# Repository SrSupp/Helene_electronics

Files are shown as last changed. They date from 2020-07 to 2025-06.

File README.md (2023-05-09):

Author: Sven Suppelt, Felix Herbst		Date: 09.05.2023


# HELENE - electronics for the low cost 6DOF robot
This repository is responsible for the electronics for the Helene robotarm. Included are the PCBs and the code to run on these. 

The robot arm has a motor control board on each of its 6 axes. The board of the lowest axis, the 1st axis, acts as ROS Serial Slave. All other axes receive their control data from the 1st axis via CAN. 

A single motor control board consists of a microcontroller (ESP32), a stepper motor driver (TMC5160), a magnetic encoder to determine the current position of the robot arm (AS5048) and a CAN transceiver. 
The 1st axis is equipped with an external magnetic encoder due to lack of space. All other axes have enough space so that the board can be mounted directly above the required magnet. 

# Folder structure
The boards are located in the folder "pcb". Here you will find the board for the external encoder and the motor control board. The source code for the boards can be found in the "code" folder. Stored there are the PlatformIO projects for the ROS Serial Slave (Helene_ESP_Master) and the other boards connected via CAN (Helene_ESP_Slave).
In the pcb folder there are two additional optional boards, the end effector board and a H-bridge with voltage converter. The end effector board has its own ESP32 with an ADC for measuring load cells. Furthermore, two outputs for servos are provided, so that grippers with integrated force measurement can be realized. The H-bridge is connected via the expansion ports on the boards and can drive motors up to 3A at 5V. It does not have its own microcontroller.

# System structure of the robot arm
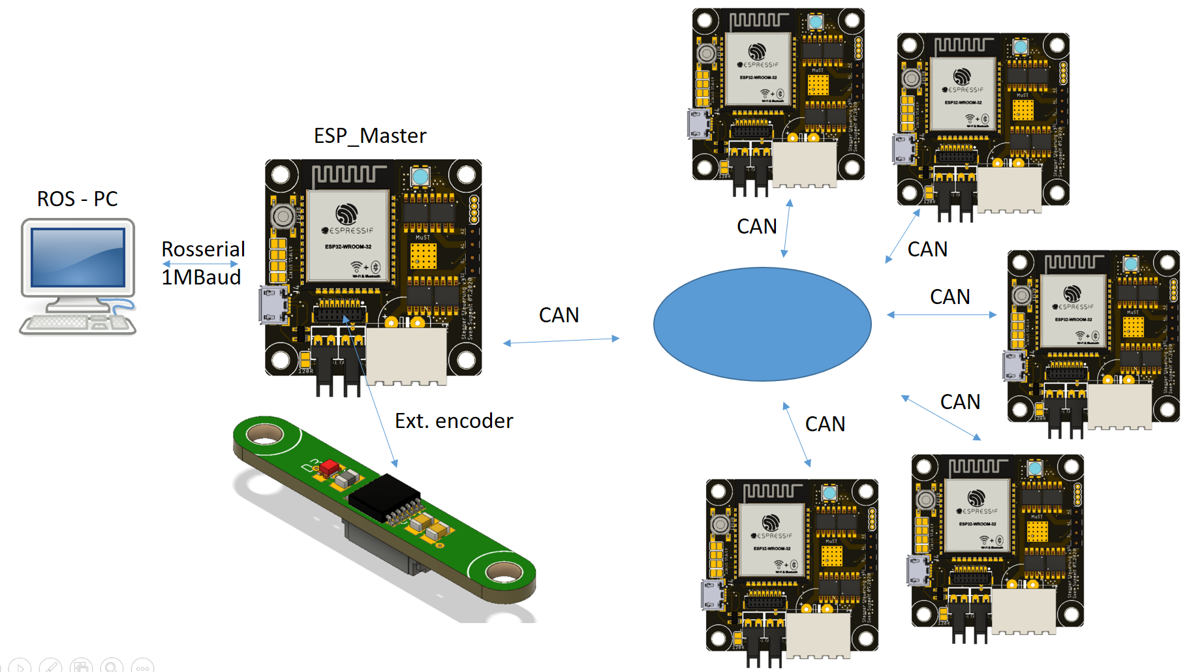
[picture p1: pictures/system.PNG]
 

# Available Serial Commands
Each slave is equipped with the possibility of serial communication. Via this interface the calibration value of each axis can be read and set and status information can be read out. It is absolutely necessary to calibrate each axis individually!
The following commands are available:

long form | short form | description
-------- | -------- | --------
*IDN? | IDN? | Prints identification
HELP? | HELP | Prints a help screen (not yet implemented)
CALSINGLEJOINT [joint ID] | CAJO [joint ID] | starts the calibration process of given joint. Instructions will be printed after that command!
SETNULL [0,1] | SENU [0,1] | globally enables (1) or disables (0) the Nullpunktfahrt at startup
GETCALVALUE [joint ID] | GECA [joint ID] | Prints the current saved calibration value of given joint
SETCALVALUE [joint ID] | SECA [joint ID] | Sets the current saved calibration value of given joint. Instructions are printed after that command!
GETACTUAL [joint ID] | GEAC [joint ID] | Prints the actual angle of given joint. The actual angle is: Raw_Angle - Calibration_Value
GETRAW [joint ID] | GERA [joint ID] | Prints the raw angle of given joint
DONULL [joint ID] | DONU [joint ID] | The given joint will do a Nullpunktfahrt
OFFANDNULL [joint ID] | OFNU [joint ID] | Sets a offset value on the current calibration value. After that a Nullpunktfahrt is initiated. Instructions are printed out!
DIAG | DIA | Prints out diagnose data

# Installation instructions

1. Gather all materials.
You will need 6 motor control boards and 1 external encoder board.
2. Do the wiring. 
You will have to run CAN and power to each motor control board. The boards are daisy-chainable!
3. Program the boards.
"Helene_ESP_Master" should be uploaded to the board in joint 1. This board is configured with rosserial so that it communicates directly with ROS.
"Helene_ESP_Slave" should be uploaded to the boards in joint 2-6. These boards talk via CAN to the board in Joint 1 and thus receive their control information. With each individual board it is possible to calibrate the robot arm. 
After programming, each board should slowly blink red!
4. Set the SMD-Jumpers.
For joints 1 and 6 the CAN terminating resistor must be set by bridging the SMD solder bridge next to the CAN sockets.
Additionally the Joint-ID must be set for each board. For this purpose four SMD pads are provided next to the USB socket. By bridging these pads the ID can be set. The data format is binary with the most significant bit first. For example the joint 5: 0 1 0 1 must be set. 
5. Calibrate the zero position
6. Enable Nullpunktfahrt globally

# Video installation instructions

The installation process is also explained in the following video.
(http://www.youtube.com/watch?v=I9vXAa9pZOI "")
Starting at 0:09 the installation of the electronics is explained. From 6:21 on the calibration is shown.

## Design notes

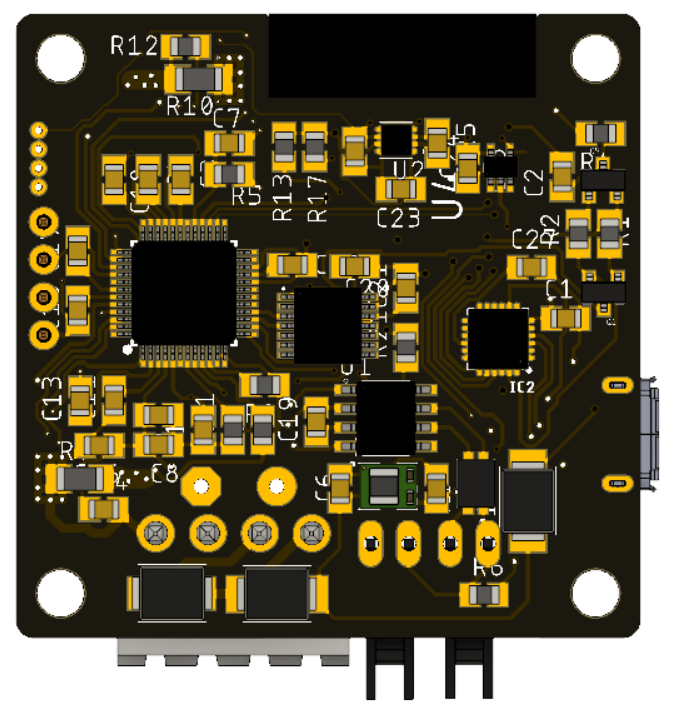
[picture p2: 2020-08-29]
pictures/Motorsteuerung_back.PNG

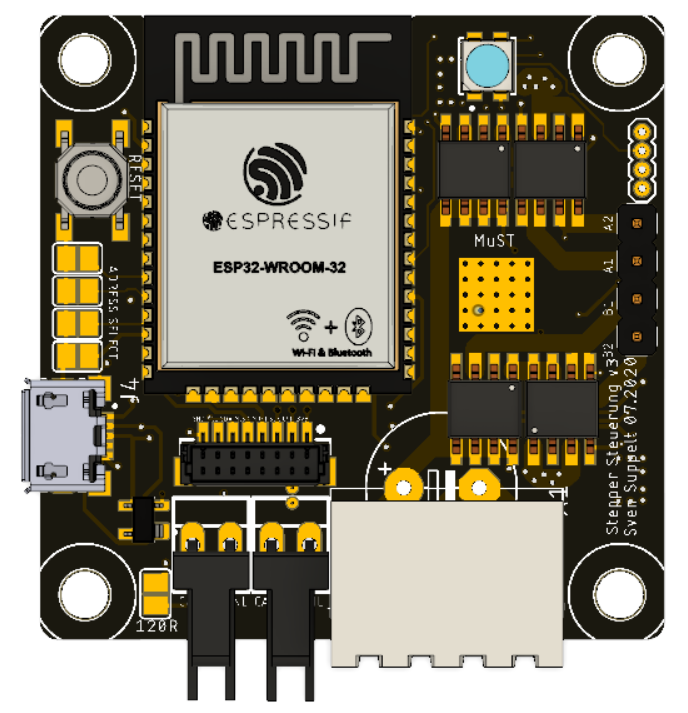
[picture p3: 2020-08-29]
pictures/Motorsteuerung_front.PNG

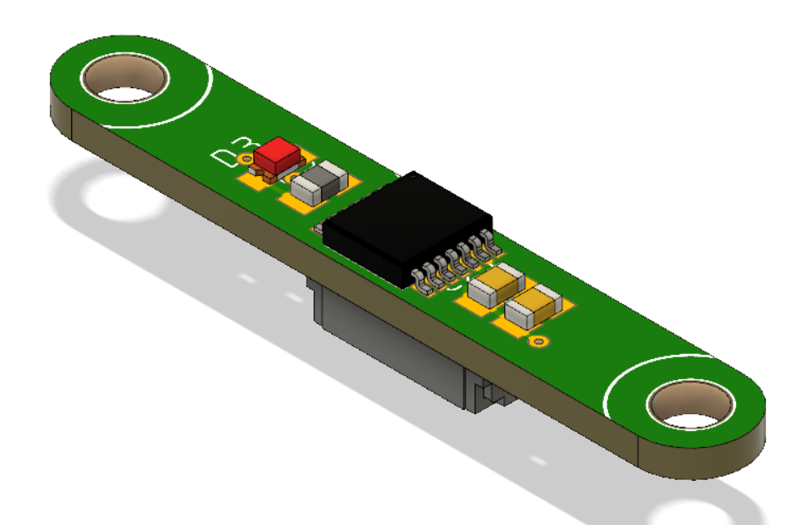
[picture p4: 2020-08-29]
pictures/ext_encoder.PNG

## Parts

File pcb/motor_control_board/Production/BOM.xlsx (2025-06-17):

 |  |  | Motorsteuerung V3 BOM
Item # | *Designator | *Qty | Manufacturer | *Mfg Part # | Description / Value | *Package/Footprint | Type | Your Instructions / Notes
1 | C1, C20 | 2 | Murata | GRM21BR6YA106KE43L | 10uF 0805 min.5V | 0805 | SMD
2 | C2, C25 | 2 | KEMET | C0805C105K4RAC7210 | 1uF 0805 min. 5V | 0805 | SMD
3 | C3 | 1 | Yageo | CC0805KRX7R0BB223 | 22nF 0805 100V | 0805 | SMD
4 | C4, C12, C13, C15, C17, C18, C19, C21, C26 | 9 | KEMET | C0805C104J5RACAUTO | 100nF 0805 | 0805 | SMD
5 | C5 | 1 | Taiyo Yuden | JMK212BJ476MG-T | 47uF 0805 min 4V | 0805 | SMD
6 | C6, C23, C24, C27 | 4 | Taiyo Yuden | UMK212BBJ475MG-T | 4,7uF 0805 min 5V | 0805 | SMD
7 | C7, C14, C16 | 3 | KEMET | C0805C474K5RAC7210 | 470nF 0805 min 25V | 0805 | SMD
8 | C8, C9 | 2 | Murata | GRM21BR6YA106KE43L | 10uF 0805 min 25V | 0805 | SMD
9 | C10, C11 | 2 | Taiyo Yuden | UMK212ABJ225KG-T | 2,2uF 0805 min 12V | 0805 | SMD
10 | C22 | 1 | Do not equip | Do not equip | Do not equip | Do not equip | THT | Do not equip
11 | R1, R2 | 2 | Yageo | RC0805FR-071KL | 1k 0805 | 0805 | SMD
12 | R4, R13, R17 | 3 | Yageo | RC0805JR-0710KL | 10k 0805 | 0805 | SMD
13 | R5 | 1 | CR0805-J/-2R2ELF | Bourns | 2,2 Ohm 0805 | 0805 | SMD
14 | R6 | 1 | Yageo | RC0805FR-07120RL | 120 Ohm 0805 | 0805 | SMD
15 | R7, R10 | 2 | Yageo | RL1206FR-070R075L | 75mOhm 1206 | 1206 | SMD | Messshunt
16 | R8, R9, R11, R12, R21 | 5 | Panasonic | ERA-6AEB49R9V | 49,9 Ohm 0805 | 0805 | SMD
17 | D1, D2 | 2 | Multicomp | SS34A | SMB Shottky Diode | SMB | SMD
18 | D3 | 1 | Adafruit Industries | 2659 | 2659 Adafruit LED | 2659 | SMD
19 | D7 | 1 | Littlefuse | SP0503BAHTG | USB ESD Schutz | SOT143 | SMD
20 | D10 | 1 | Diodes Inc. | SMBJ30AQ-13-F | TVS Diode | SMBJ | SMD
21 | IC1 | 1 | Trinamic | TMC5160-TA-T | Motortreiber IC | TQFP48-EP | SMD
22 | IC2 | 1 | Solicon Labs | CP2104-F03-GM | USB Seriell Wandler | QFN24_4MM_SMSC | SMD
23 | J1 | 1 | Do not equip | Do not equip | Do not equip | Do not equip | THT
24 | J2 | 1 | JST | BM08B-SRSS-TB(LF)(SN) | 8 Port SMD stehende Buchse |  | SMD
25 | J3 | 1 | Do not equip | Do not equip | Do not equip | Do not equip | THT
27 | J4 | 1 | Amphenol FCI | 10118193-0001LF | USB-Stecker 5P MICRO USB TYPE B RECEPTACLE W/ PEGS | FCI_10118193-0001LF | SMD
28 | PS1 | 1 | Texas Instruments | LMZM23600V3SILR | 3,3V Spannungswandler |  | SMD
29 | Q1, Q2, Q3, Q4 | 4 | Alpha&Omega | AO4882 | Dual N-Ch Mosfet | SOIC8 | SMD
30 | Q5, Q6 | 2 | ON Semiconductor | BC817-16LT1G | NPN Transistor | SOT23-3 | SMD
31 | SJ1, SJ2 | 2 | Do not equip | Do not equip | Do not equip | Do not equip | SMD | Do not equip
32 | SJ5, SJ6, SJ7, SJ8, SJ9 | 5 | Do not equip | Do not equip | Do not equip | Do not equip | SMD | Do not equip
33 | SW1 | 1 | E-Switch | TL3342F160QG | Taster |  | SMD
34 | U1 | 1 | Texas Instruments | SN65HVD232DR | Can Treiber | SOIC127P600X175-8N | SMD
35 | U2 | 1 | Texas Instruments | LM2775QDSGTQ1 | 3,3V zu 5v | SON50P200X200X80-9N | SMD
36 | U3 | 1 | ams | AS5048A-HTSP-500 | Magnetencoder | SOP65P640X120-14N | SMD
37 | U4 | 1 | Nexperia | 74HCT1G08GW,125 | And Gate | SOT65P210X110-5N | SMD
38 | X1 | 1 | Do not equip | Do not equip | Do not equip | Do not equip | THT | Do not equip
39 | X2 | 1 | Espressif Systems | ESP32-WROOM-32 | Microprozessor |  | SMD
40 | X6, X7 | 2 | Do not equip | Do not equip | Do not equip | Do not equip | THT | Do not equip
41 | FL1 | 1 | Murata | DLW32SH220XK2L | Gleichtaktdrosseln / Filter 1210 80VDC 22uH 250mA AEC-Q200 | 1210 | SMD

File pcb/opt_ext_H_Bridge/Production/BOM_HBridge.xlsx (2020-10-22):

 |  |  | External H Bridge BOM
Item # | *Designator | *Qty | Manufacturer | *Mfg Part # | Description / Value | *Package/Footprint | Type | Your Instructions / Notes
1 | C20 | 1 | Murata | GRM21BR6YA106KE43L | 10uF 0805 min.5V | 0805 | SMD
2 | C21 | 1 | KEMET | C0805C104J5RACAUTO | 100nF 0805 | 0805 | SMD
3 | U4 | 1 | Nexperia | 74LVC1G08GW,125 | And Gate | SOT65P210X110-5N | SMD
4 | J1,J2 | 2 | JST | BM08B-SRSS-TB(LF)(SN) | 8 Port SMD stehende Buchse |  | SMD
5 | U10 | 1 | ON Semiconductor | LM2576D2TR4-5G | Schaltspannungsregler 5V 3A Buck PWM |  | SMD
6 | L1 | 1 | Coilcraft | MSS1038T-104MLC | Festinduktivitäten 100uH Shld 20% 1.45A 304mOhms AECQ2 |  | SMD
7 | D4 | 1 | Vishay Semiconductors | SS36-E3/57T | Schottky Dioden & Gleichrichter 3.0 Amp 60 Volt |  | SMD
8 | C1,C31 | 2 | Nichicon | UCW1V221MNL1GS | Alu-Elektrolytkondensatoren - SMD 35volts 220uF AEC-Q200 |  | SMD
9 | U1 | 1 | Microchip Technology | TC4427VOA713 | Gate-Treiber 1.5A Dual |  | SMD
10 |  | 1 | Phoenix Contact | 1984617 | TERM BLK 2POS SIDE ENT 3.5MM PCB |  | THT
11 |  | 1 | Metz Connect | 31182104 | 4 Pos Header |  | THT
12 |  | 1 | JST Sales America Inc. | A08SR08SR30K152A | JUMPER 08SR-3S - 08SR-3S 6" |  | Kabel
13 |  | 2 | Metz Connect | 31169102 | 2 Pos Screw Terminal |  | Connector

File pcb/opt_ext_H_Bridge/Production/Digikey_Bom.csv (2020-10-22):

Manufacturer Part Number | Manufacturer | Digi-Key Part Number | Customer Reference | Reference Designator | Packaging | Part Status | Quantity | Unit Price | Extended Price | Quantity Available | Mfg Std Lead Time | Description | RoHS Status | Lead Free Status | REACH Status
74LVC1G08GW,125 | Nexperia USA Inc. | 1727-2872-1-ND |  |  | Cut Tape (CT) | Active | 1 | 0,18000 | 0,18 € | 27759 | 4 Weeks | IC GATE AND 1CH 2-INP 5TSSOP | ROHS3 Compliant | Lead free | REACH Unaffected
BM08B-SRSS-TB(LF)(SN) | JST Sales America Inc. | 455-1794-1-ND |  |  | Cut Tape (CT) | Active | 2 | 0,72000 | 1,44 € | 12416 | 16 Weeks | CONN HEADER SMD 8POS 1MM | RoHS Compliant | Lead free | Not Available
LM2576D2TR4-5G | ON Semiconductor | LM2576D2TR4-5GOSCT-ND |  |  | Cut Tape (CT) | Active | 1 | 1,97000 | 1,97 € | 1873 | 9 Weeks | IC REG MULTI CONFG 5V 3A D2PAK-5 | ROHS3 Compliant | Lead free | REACH Unaffected
SS36-E3/57T | Vishay Semiconductor Diodes Division | SS36-E3/57TGICT-ND |  |  | Cut Tape (CT) | Active | 1 | 0,43000 | 0,43 € | 11334 | 8 Weeks | DIODE SCHOTTKY 60V 3A DO214AB | ROHS3 Compliant | Lead free | REACH Unaffected
UCW1V221MNL1GS | Nichicon | 493-9430-1-ND |  |  | Cut Tape (CT) | Active | 2 | 0,60000 | 1,20 € | 28323 | 16 Weeks | CAP ALUM 220UF 20% 35V SMD | ROHS3 Compliant | Lead free | REACH Unaffected
TC4427VOA713 | Microchip Technology | TC4427VOA713CT-ND |  |  | Cut Tape (CT) | Active | 2 | 1,12000 | 2,24 € | 1871 | 8 Weeks | IC GATE DRVR LOW-SIDE 8SOIC | ROHS3 Compliant | Lead free | REACH Unaffected
1984617 | Phoenix Contact | 277-1721-ND |  |  | Box | Active | 1 | 0,41000 | 0,41 € | 12907 | 7 Weeks | TERM BLK 2POS SIDE ENT 3.5MM PCB | RoHS Compliant | Lead free | Not Available
A08SR08SR30K152A | JST Sales America Inc. | 455-3004-ND |  |  | Bulk | Active | 1 | 1,63000 | 1,63 € | 1113 | 12 Weeks | JUMPER 08SR-3S - 08SR-3S 6" | RoHS Compliant | Lead free | Not Available
CDRH10D60BT150NP-101MC | Sumida America Components Inc. | 308-CDRH10D60BT150NP-101MCCT-ND |  |  | Cut Tape (CT) | Active | 1 | 1,61000 | 1,61 € | 500 | Not Available | FIXED IND 100UH 2.3A 160MOHM SMD | ROHS3 Compliant | Not Available | Not Available

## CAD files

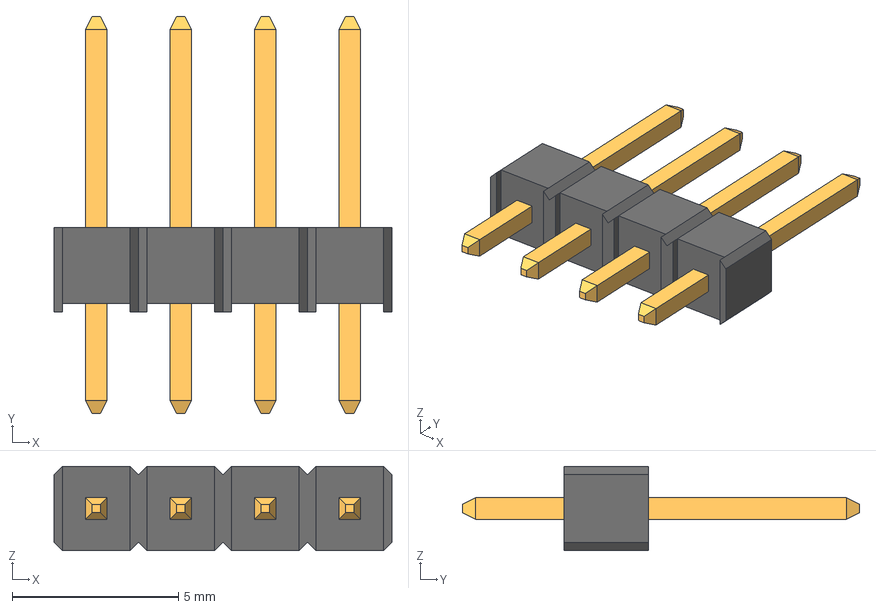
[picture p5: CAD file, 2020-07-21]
pcb/end_effector_board/PCB/zl201-4_p2-54_l10-2_w2-54_h8-89.stp
10.2 x 11.9 x 2.54 mm

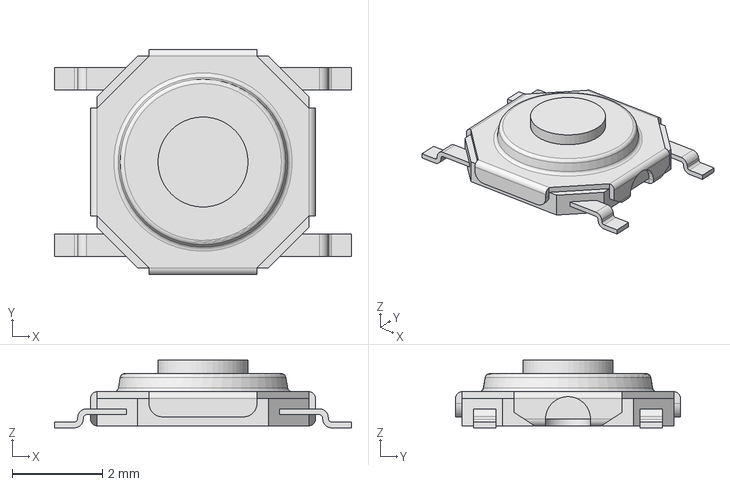
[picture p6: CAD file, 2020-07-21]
pcb/end_effector_board/PCB/TL3342FxxxQG.stp
6.60 x 5.00 x 1.50 mm

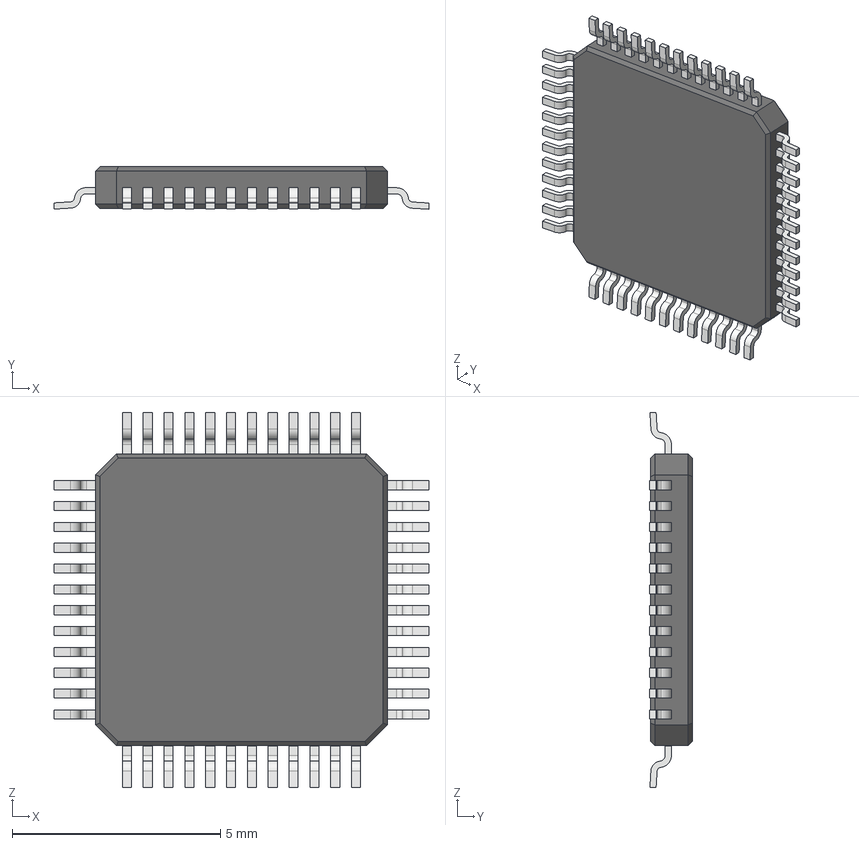
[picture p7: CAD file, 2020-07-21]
pcb/end_effector_board/PCB/TQFP48.step
9.00 x 1.02 x 9.01 mm

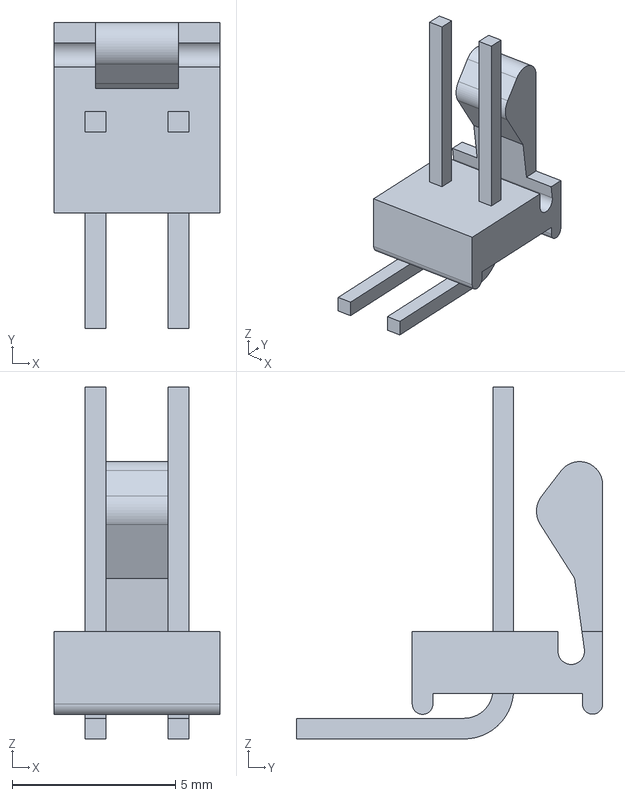
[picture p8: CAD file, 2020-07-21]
pcb/end_effector_board/PCB/c-640457-2-w-3d.stp
5.08 x 9.40 x 10.8 mm

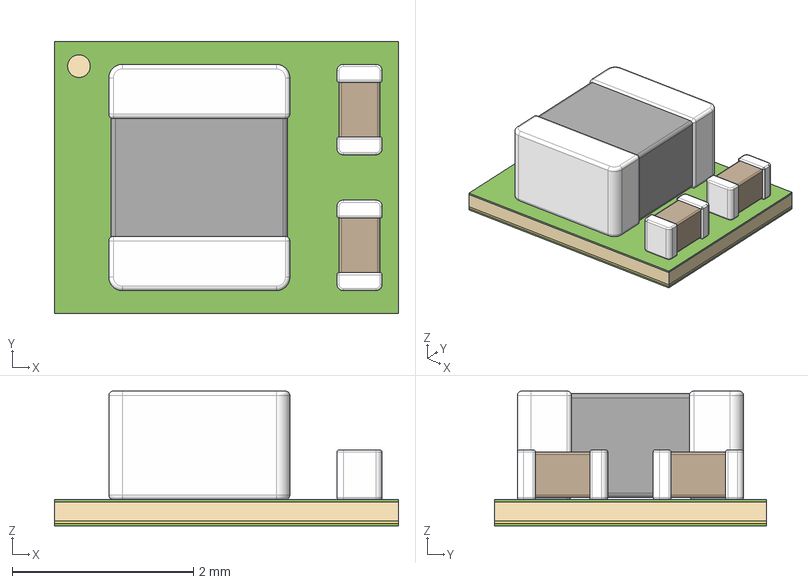
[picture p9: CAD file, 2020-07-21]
pcb/end_effector_board/PCB/LMZM23600.stp
3.80 x 3.00 x 1.49 mm
SOLDERMASK-BTM-SIL0010A
METAL-SIP
SUBSTRATE-SIP
SOLDERMASK-TOP
INDUCTOR-BODY
INDUCTOR-TERMNL x 2
CAP-BODY x 2
CAP-TERMNL x 4

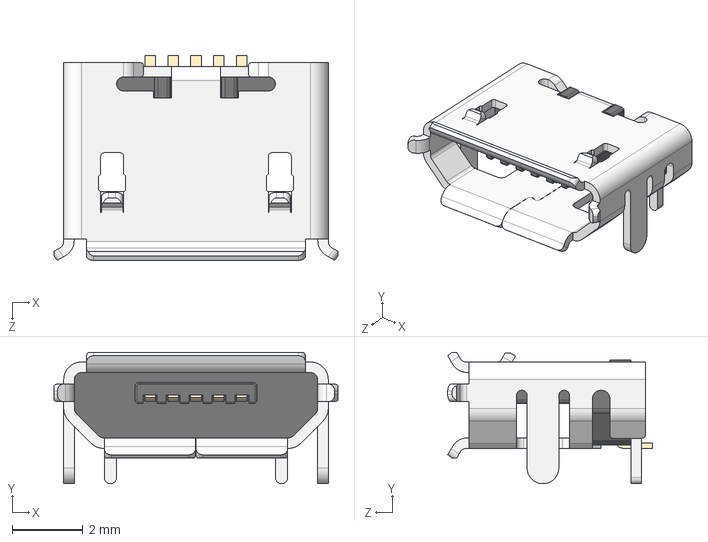
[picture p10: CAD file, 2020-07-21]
pcb/end_effector_board/PCB/Micro USB-B Female 5Pin SMD.STEP
8.05 x 3.73 x 5.80 mm

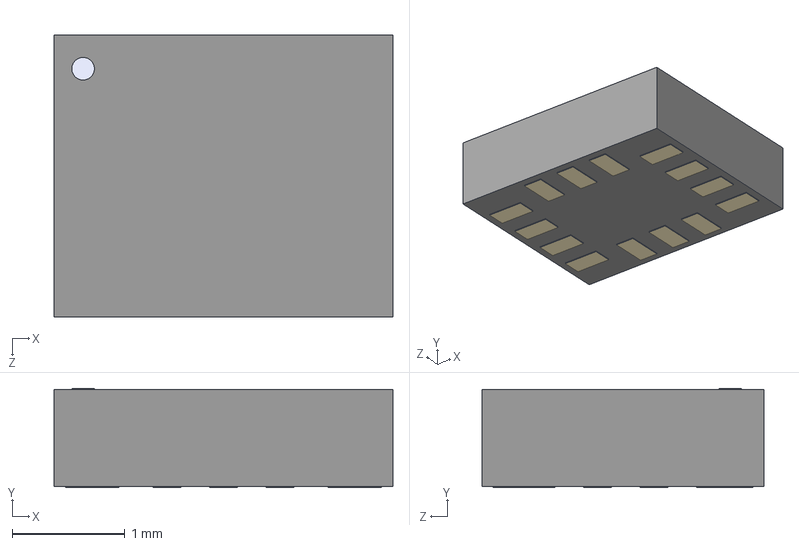
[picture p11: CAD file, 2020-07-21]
pcb/end_effector_board/PCB/LGA14.STEP
3.00 x 0.88 x 2.50 mm

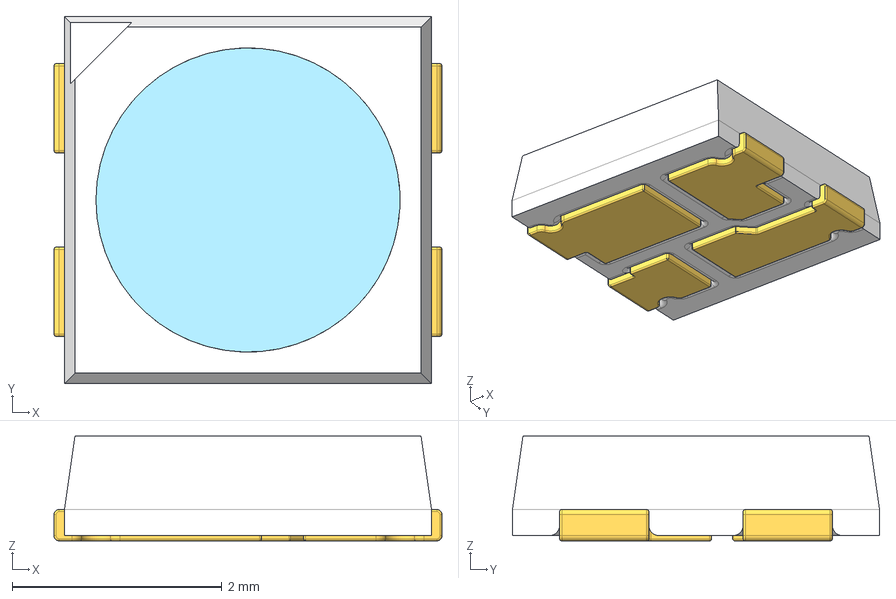
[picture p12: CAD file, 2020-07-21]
pcb/end_effector_board/PCB/SMD3535 RGB.stp
3.70 x 3.50 x 1.00 mm

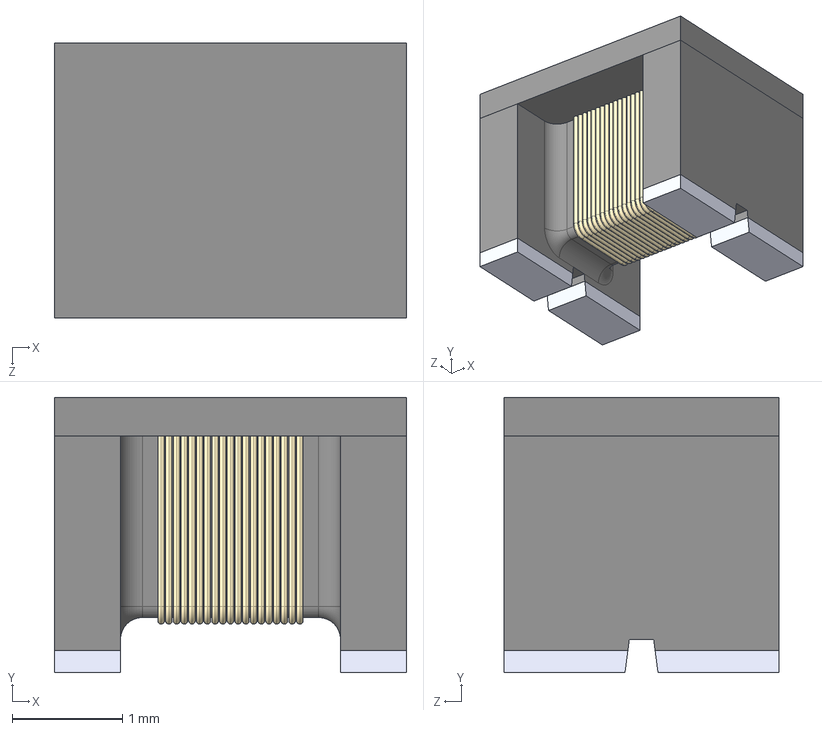
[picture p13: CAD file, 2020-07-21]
pcb/end_effector_board/PCB/DLW32SH110XK2L--3DModel-STEP-1.STEP
3.20 x 2.50 x 2.50 mm

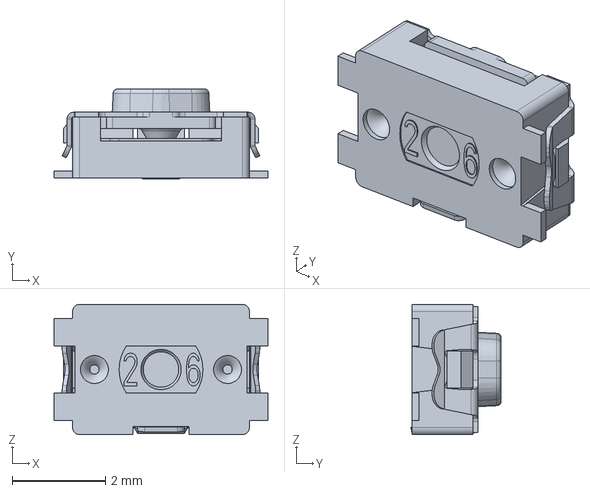
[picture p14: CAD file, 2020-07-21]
pcb/end_effector_board/PCB/KMR231GLFS.stp
4.60 x 1.94 x 2.80 mm

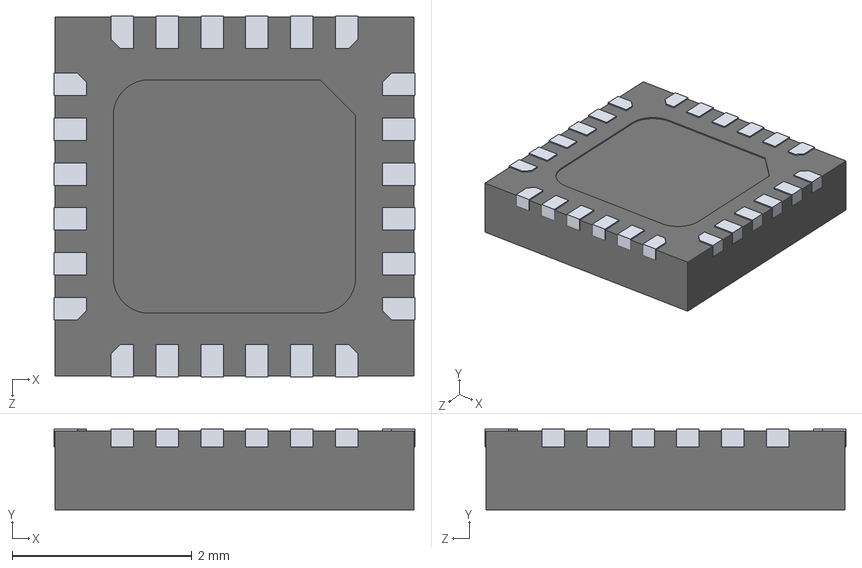
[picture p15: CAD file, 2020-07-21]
pcb/end_effector_board/PCB/QFN24(4X4).STEP
4.02 x 0.9 x 4.02 mm

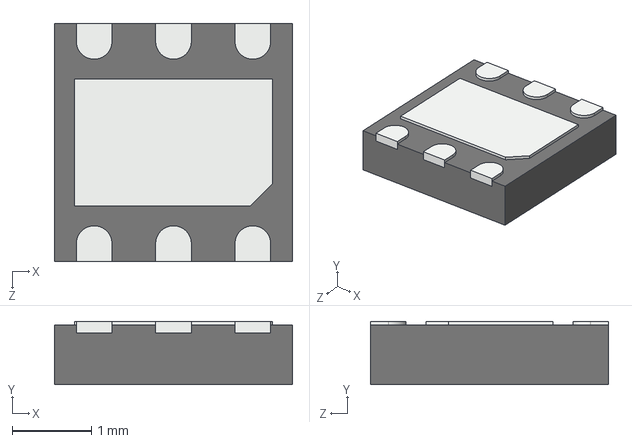
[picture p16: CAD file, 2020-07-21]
pcb/end_effector_board/PCB/User Library-DFN6-3x3x0_80.step
3.00 x 0.8 x 3.00 mm

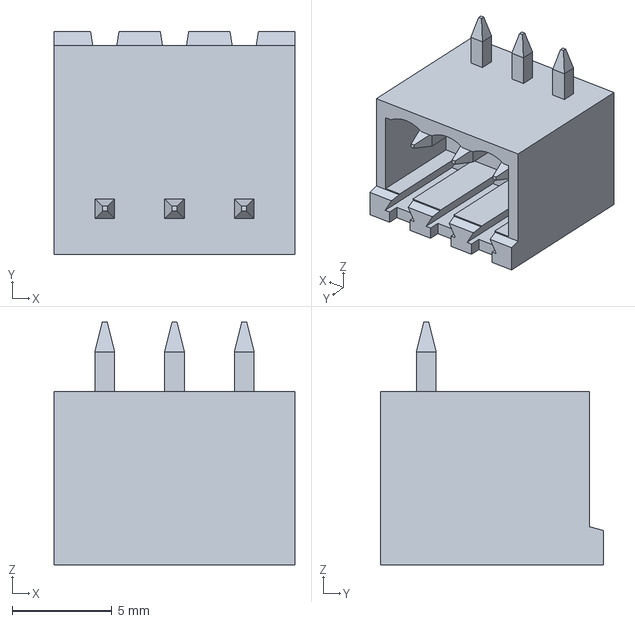
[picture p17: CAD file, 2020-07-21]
pcb/end_effector_board/PCB/31182103.stp
12.1 x 11.2 x 12.2 mm

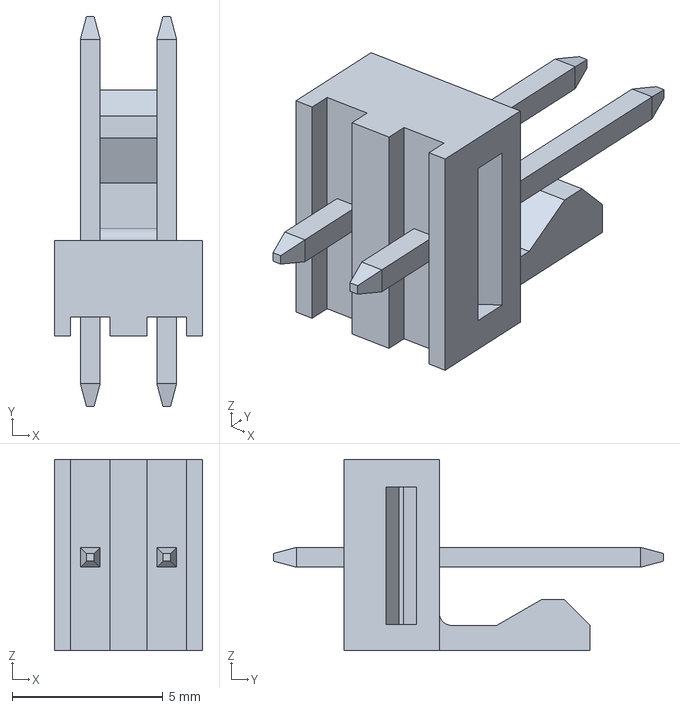
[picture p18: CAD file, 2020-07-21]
pcb/end_effector_board/PCB/1718560002.stp
4.93 x 13.0 x 6.35 mm

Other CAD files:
pcb/end_effector_board/PCB/022032021.stp
pcb/end_effector_board/PCB/10147605-8P.stp
pcb/end_effector_board/PCB/10118193-0001LF--3DModel-STEP-56544.STEP
pcb/end_effector_board/PCB/31182104.stp
pcb/end_effector_board/PCB/31183103.stp

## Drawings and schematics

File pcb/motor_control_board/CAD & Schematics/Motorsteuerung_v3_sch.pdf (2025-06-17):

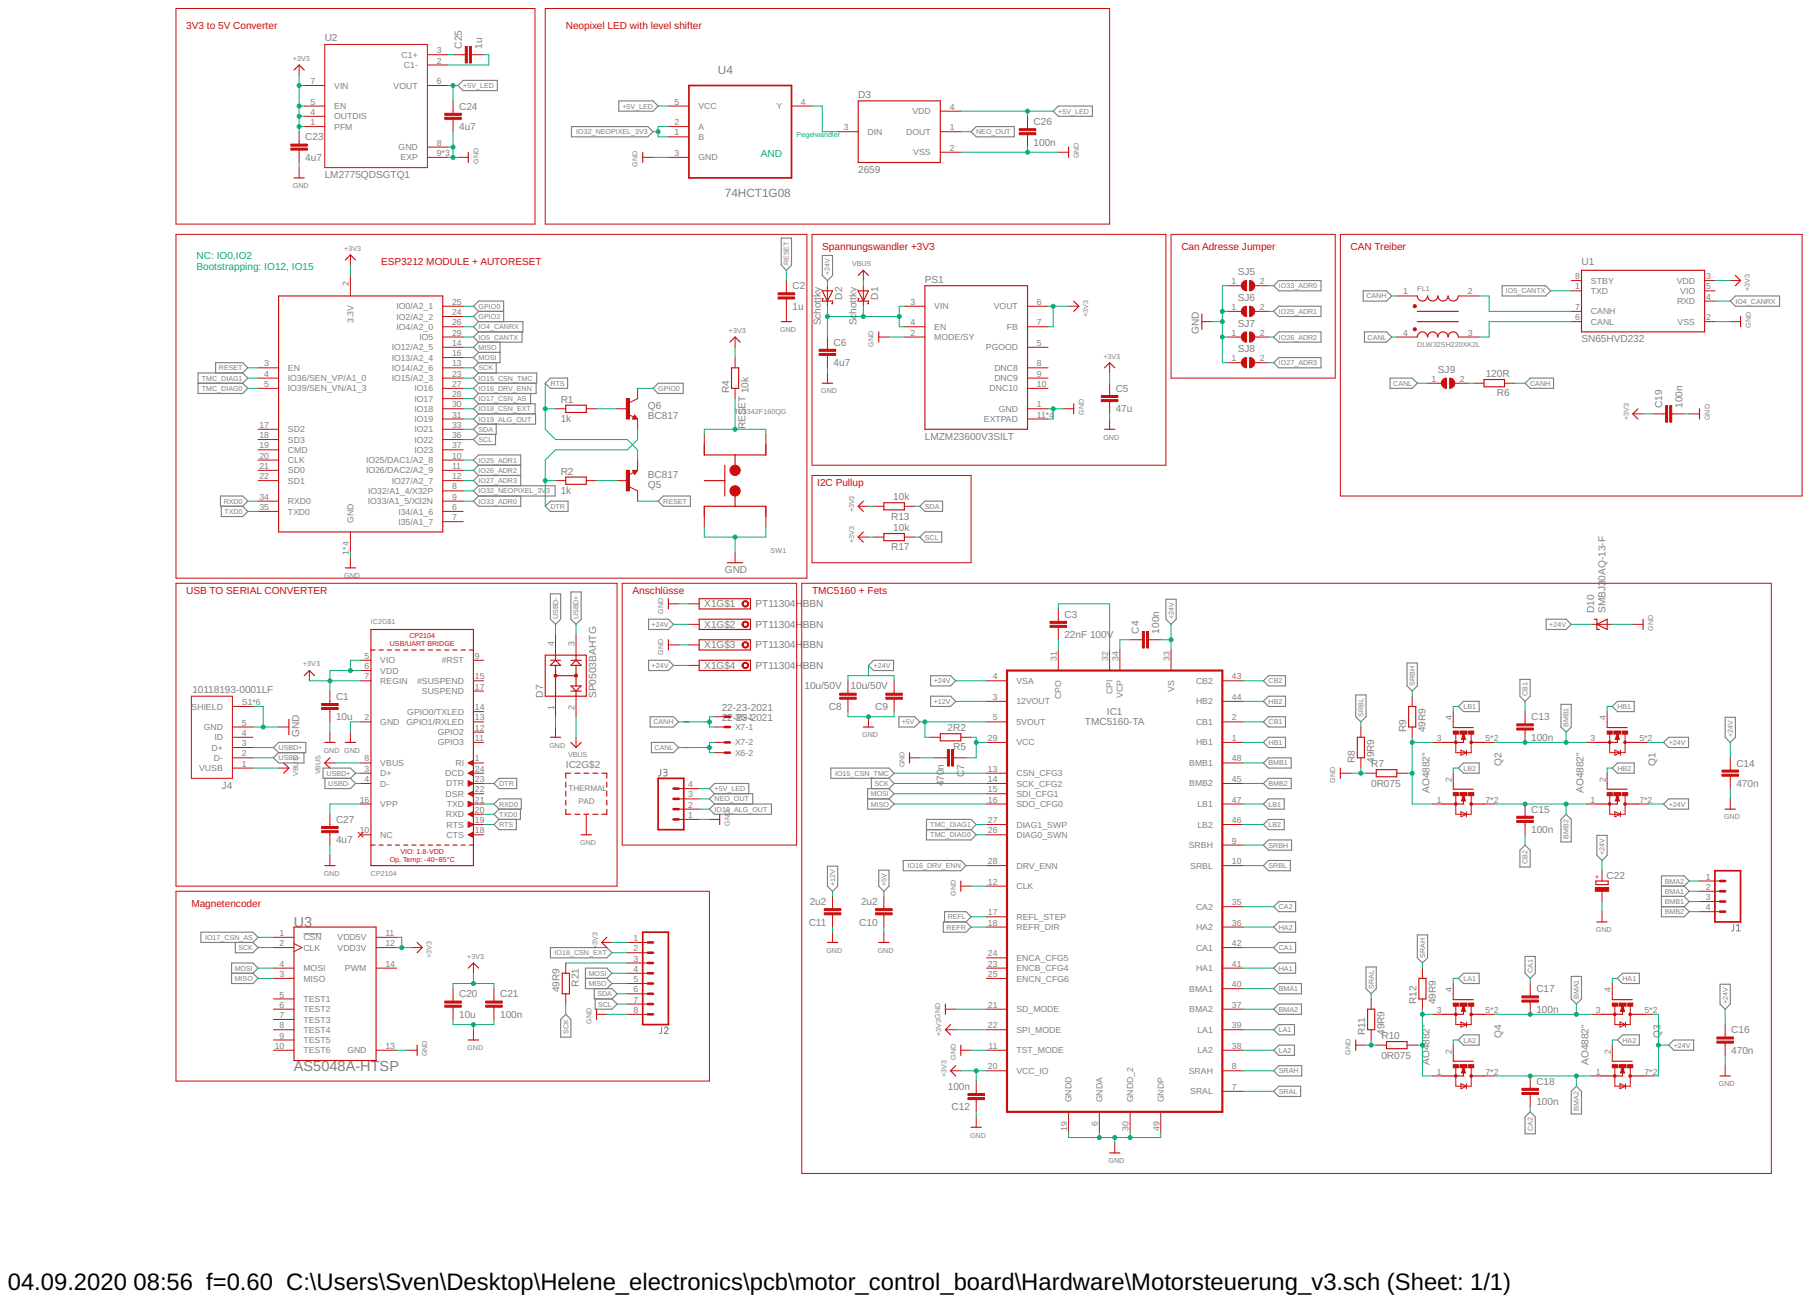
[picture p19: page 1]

USB TO SERIAL CONVERTER

VIO: 1.8-VDD Op. Temp: -40~85°C

04.09.2020 08:56 f=0.60 C:\Users\Sven\Desktop\Helene_electronics\pcb\motor_control_board\Hardware\Motorsteuerung_v3.sch (Sheet: 1/1)

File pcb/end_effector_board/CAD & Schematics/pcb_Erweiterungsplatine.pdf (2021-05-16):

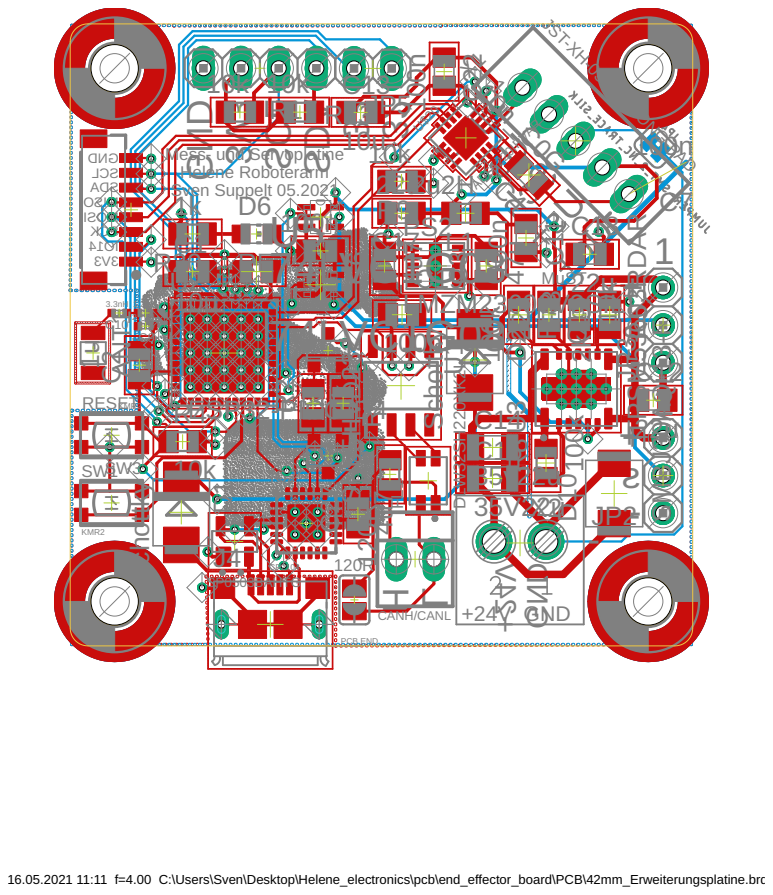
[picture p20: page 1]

JST-XH-05-PIN-LONG-PAD

Ud- Us- Sch Us+ Ud+

16.05.2021 11:11 f=4.00 C:\Users\Sven\Desktop\Helene_electronics\pcb\end_effector_board\PCB\42mm_Erweiterungsplatine.brd

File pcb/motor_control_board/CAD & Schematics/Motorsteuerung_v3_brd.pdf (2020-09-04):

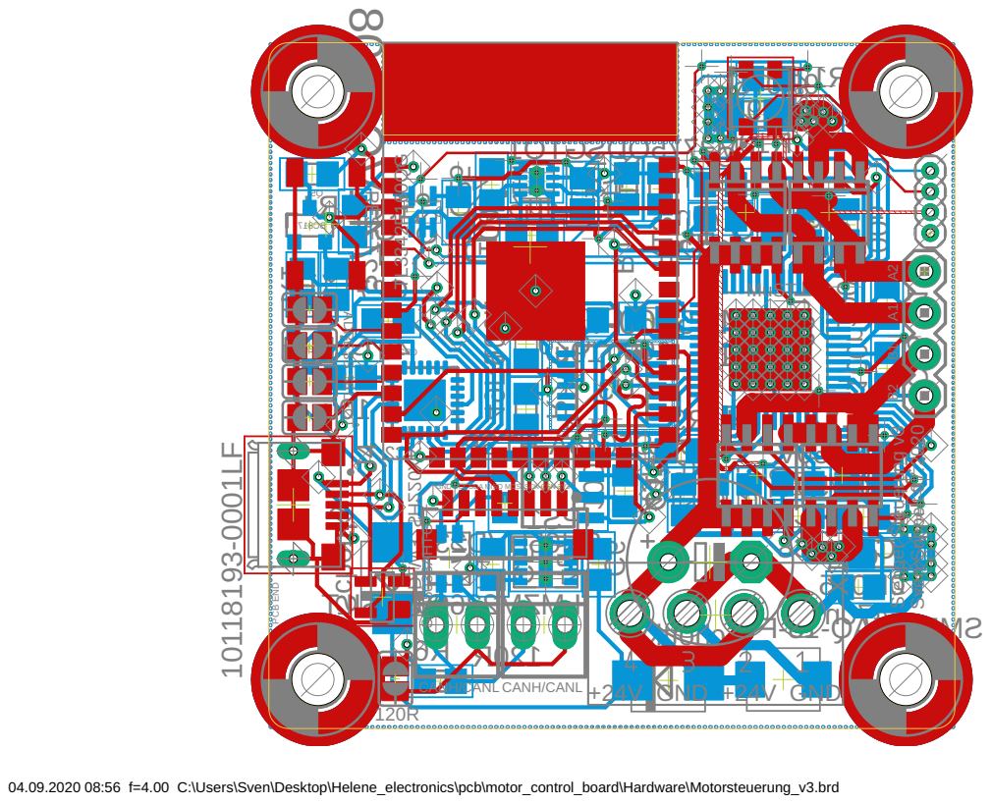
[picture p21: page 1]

04.09.2020 08:56 f=4.00 C:\Users\Sven\Desktop\Helene_electronics\pcb\motor_control_board\Hardware\Motorsteuerung_v3.brd

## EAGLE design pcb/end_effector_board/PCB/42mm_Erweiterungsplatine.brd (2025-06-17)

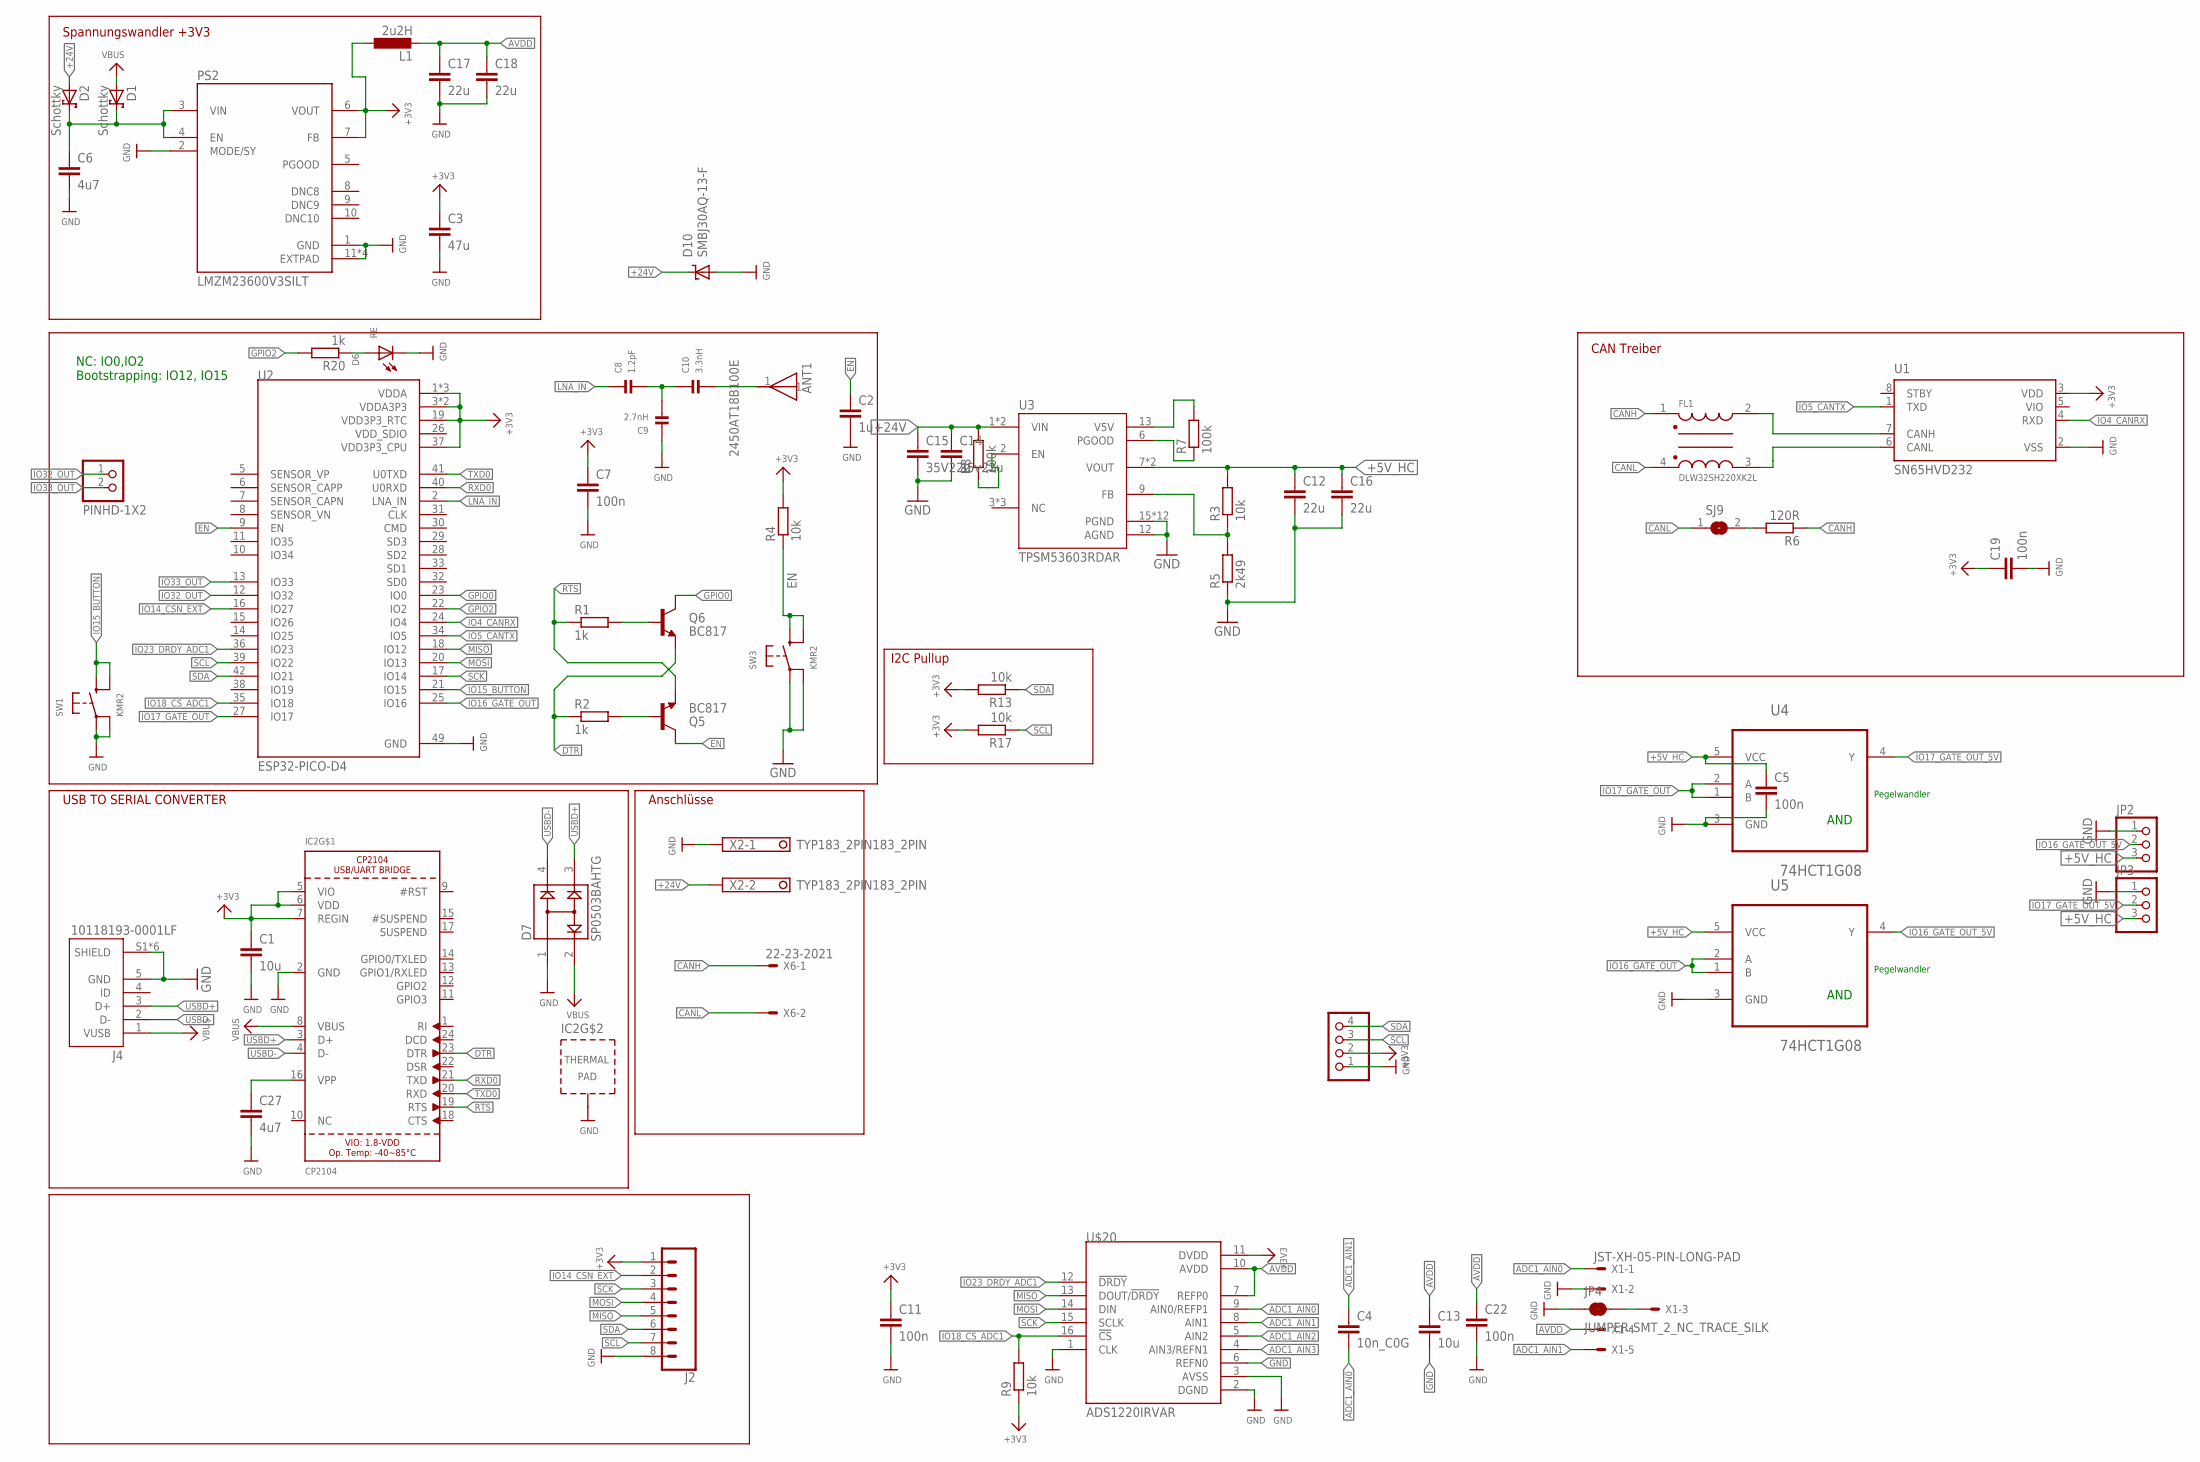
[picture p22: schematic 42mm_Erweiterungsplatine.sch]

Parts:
ANT1: 2450AT18B100E; ANT_2450AT18B100E
C1, C13: 10u; C0805
C2: 1u; C0805
C3: 47u; C0805
C4: 10n_C0G; C0805
C5, C7, C11, C19, C22: 100n; C0805
C6, C27: 4u7; C0805
C8: 1.2pF; _0402MP
C9: 2.7nH; _0402MP
C10: 3.3nH; _0402MP
C12, C16, C17, C18: 22u; C0805
C14: 35v22u; C1206
C15: 35V22u; C1206
D1, D2: Schottky; SMB
D6: RE; CHIP-LED0805
D7: SP0503BAHTG; SOT143
D10: SMBJ30AQ-13-F; SMBJ
FL1: DLW32SH220XK2L; FIL_DLW32SH110XK2L
IC2: CP2104; QFN24_4MM_SMSC
J2: CONN_08BM08B-SRSS-TB; BM08B-SRSS-TB
J4: 10118193-0001LF; FCI_10118193-0001LF
JP1: PINHD-1X4; 1X04
JP2, JP3: PINHD-1X3; 1X03
JP4: JUMPER-SMT_2_NC_TRACE_SILK; SMT-JUMPER_2_NC_TRACE_SILK
JP5: PINHD-1X2; 1X02
L1: 2u2H; L0805
PS2: LMZM23600V3SILT; CONV_LMZM23600V3SILT
Q5, Q6: BC817; SOT23-3
R1, R2, R20: 1k; R0805
R3, R4, R9, R13, R17: 10k; R0805
R5: 2k49; R0805
R6: 120R; R0805
R7, R8: 100k; R0805
SJ9: SJ
SW1, SW3: KMR2; BTN_KMR2_4.6X2.8
U1: SN65HVD232; SOIC127P600X175-8N
U2: ESP32-PICO-D4; PQFN50P700X700X104-49N
U3: TPSM53603RDAR; IC_TPSM53603RDAR
U4, U5: 74HCT1G08; SOT65P210X110-5N
U$20: ADS1220IRVAR; QFN50P350X350X100-17N214X214
X1: JST-XH-05-PIN-LONG-PAD; JST-XH-05-PACKAGE-LONG-PAD
X2: TYP183_2PIN183_2PIN; TYP183_FT_2PIN
X6: 22-23-2021

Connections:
3.3V: R9.1
+3V3: C1.1, C3.1, C7.1, C11.1, C19.1, IC2.5 (VIO), IC2.6 (VDD), IC2.7 (REGIN), J2.1, JP1.2, L1.1, PS2.6 (VOUT), PS2.7 (FB), R4.2, R13.2, R17.2, U1.3 (VDD), U2.1 (VDDA), U2.3 (VDDA3P3), U2.4 (VDDA3P3), U2.19 (VDD3P3_RTC), U2.37 (VDD3P3_CPU), U2.43 (VDDA), U2.46 (VDDA), U$20.11 (DVDD)
+5V_HC: C5.1, C12.1, C16.1, JP2.3, JP3.3, R3.2, U3.7 (VOUT), U3.8 (VOUT), U4.5 (VCC), U5.5 (VCC)
+24V: C14.1, C15.1, D2.A, D10.C, R8.2, U3.1 (VIN), U3.14 (VIN), X2.2
ADC1_AIN0: C4.2, U$20.9 (AIN0/REFP1), X1.1
ADC1_AIN1: C4.1, U$20.8 (AIN1), X1.5
ADC1_AIN2: U$20.5 (AIN2)
ADC1_AIN3: U$20.4 (AIN3/REFN1)
AVDD: C13.1, C17.1, C18.1, C22.1, L1.2, U$20.7 (REFP0), U$20.10 (AVDD), X1.4
CANH: FL1.1, R6.1, X6.1
CANL: FL1.4, SJ9.1, X6.2
DTR: IC2.23 (DTR), Q6.2 (E), R2.1
EN: C2.1, Q5.3 (C), R4.1, SW3.B (S), SW3.B' (S1), U2.9 (EN)
GND: C1.2, C2.2, C3.2, C5.2, C6.2, C7.2, C9.1, C11.2, C12.2, C13.2, C14.2, C15.2, C16.2, C17.2, C18.2, C19.2, C22.2, C27.2, D6.C, D7.1, D10.A, IC2.2 (GND), IC2.THERM (TP), J2.8, J4.5 (GND), J4.S1 (SHIELD), J4.S2 (SHIELD), J4.S3 (SHIELD), J4.S4 (SHIELD), J4.S5 (SHIELD), J4.S6 (SHIELD), JP1.1, JP2.1, JP3.1, JP4.1, PS2.1 (GND), PS2.2 (MODE/SY), PS2.11 (EXTPAD), PS2.11_1 (EXTPAD), PS2.11_2 (EXTPAD), PS2.11_3 (EXTPAD), R5.1, SW1.A, SW1.A' (P1), SW3.A, SW3.A' (P1), U1.2 (VSS), U2.49 (GND), U3.12 (AGND), U3.15 (PGND), U3.15_1 (PGND), U3.15_2 (PGND), U3.15_3 (PGND), U3.15_4 (PGND), U3.15_5 (PGND), U3.15_6 (PGND), U3.15_7 (PGND), U3.15_8 (PGND), U3.15_9 (PGND), U3.15_10 (PGND), U3.15_11 (PGND), U4.3 (GND), U5.3 (GND), U$20.1 (CLK), U$20.2 (DGND), U$20.3 (AVSS), U$20.6 (REFN0), X1.2, X2.1
GPIO0: Q6.3 (C), U2.23 (IO0)
GPIO2: R20.2, U2.22 (IO2)
IO4_CANRX: U1.4 (RXD), U2.24 (IO4)
IO5_CANTX: U1.1 (TXD), U2.34 (IO5)
IO14_CSN_EXT: J2.2, U2.16 (IO27)
IO15_BUTTON: SW1.B (S), SW1.B' (S1), U2.21 (IO15)
IO16_GATE_OUT: U2.25 (IO16), U5.1 (B), U5.2 (A)
IO16_GATE_OUT_5V: JP2.2, U5.4 (Y)
IO17_GATE_OUT: U2.27 (IO17), U4.1 (B), U4.2 (A)
IO17_GATE_OUT_5V: JP3.2, U4.4 (Y)
IO18_CS_ADC1: R9.2, U2.35 (IO18), U$20.16 (!CS)
IO23_DRDY_ADC1: U2.36 (IO23), U$20.12 (!DRDY)
IO32_OUT: JP5.1, U2.12 (IO32)
IO33_OUT: JP5.2, U2.13 (IO33)
LNA_IN: C8.1, U2.2 (LNA_IN)
MISO: J2.5, U2.18 (IO12), U$20.13 (DOUT/!DRDY)
MOSI: J2.4, U2.20 (IO13), U$20.14 (DIN)
unnamed: C6.1, D1.C, D2.C, PS2.3 (VIN), PS2.4 (EN)
unnamed: C8.2, C9.2, C10.1
unnamed: ANT1.1, C10.2
unnamed: R3.1, R5.2, U3.9 (FB)
unnamed: D6.A, R20.1
unnamed: R8.1, U3.2 (EN)
unnamed: JP4.2, X1.3
unnamed: FL1.2, U1.7 (CANH)
unnamed: FL1.3, U1.6 (CANL)
unnamed: Q5.1 (B), R2.2
unnamed: Q6.1 (B), R1.2
unnamed: R7.2, U3.13 (V5V)
unnamed: R7.1, U3.6 (PGOOD)
unnamed: R6.2, SJ9.2
unnamed: C27.1, IC2.16 (VPP)
RTS: IC2.19 (RTS), Q5.2 (E), R1.1
RXD0: IC2.21 (TXD), U2.40 (U0RXD)
SCK: J2.3, U2.17 (IO14), U$20.15 (SCLK)
SCL: J2.7, JP1.3, R17.1, U2.39 (IO22)
SDA: J2.6, JP1.4, R13.1, U2.42 (IO21)
TXD0: IC2.20 (RXD), U2.41 (U0TXD)
USBD+: D7.3, IC2.3 (D+), J4.3 (D+)
USBD-: D7.4, IC2.4 (D-), J4.2 (D-)
VBUS: D1.A, D7.2, IC2.8 (VBUS), J4.1 (VUSB)
VDD_SDIO: U2.26 (VDD_SDIO)
VIO: U1.5 (VIO)

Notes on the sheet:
USB TO SERIAL CONVERTER
NC: IO0,IO2 Bootstrapping: IO12, IO15
CAN Treiber
Anschlüsse
I2C Pullup
Spannungswandler +3V3
Pegelwandler
AND

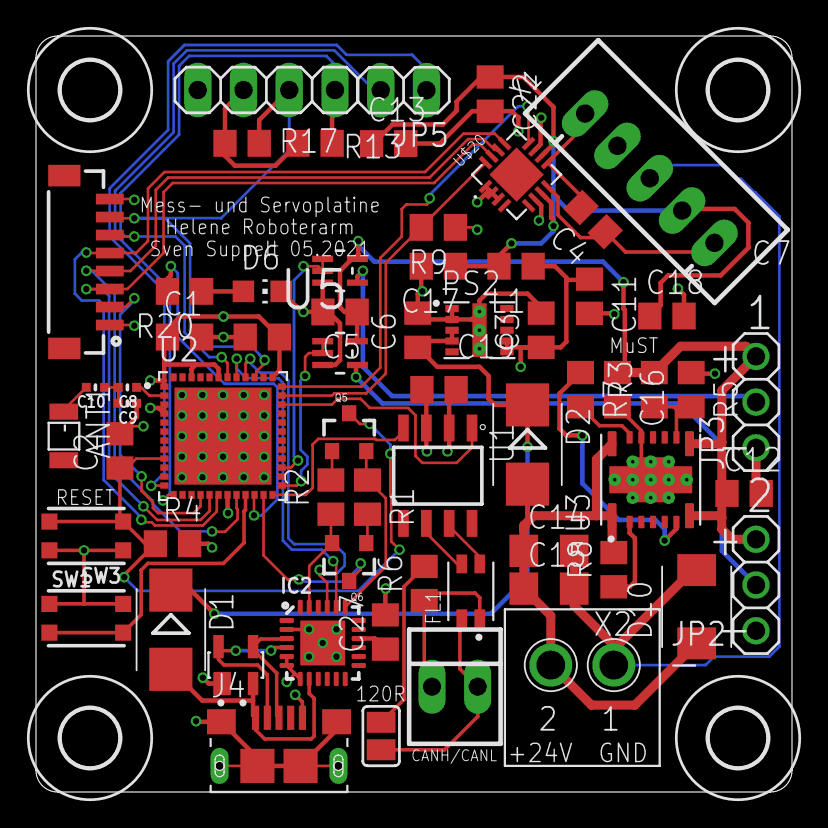
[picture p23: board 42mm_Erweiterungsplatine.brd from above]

Board: 4 copper layers, 42.0 x 42.0 mm, 68 parts (1 on the bottom side), 52 nets.

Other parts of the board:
U$1, U$2, U$3, U$4: 3,2

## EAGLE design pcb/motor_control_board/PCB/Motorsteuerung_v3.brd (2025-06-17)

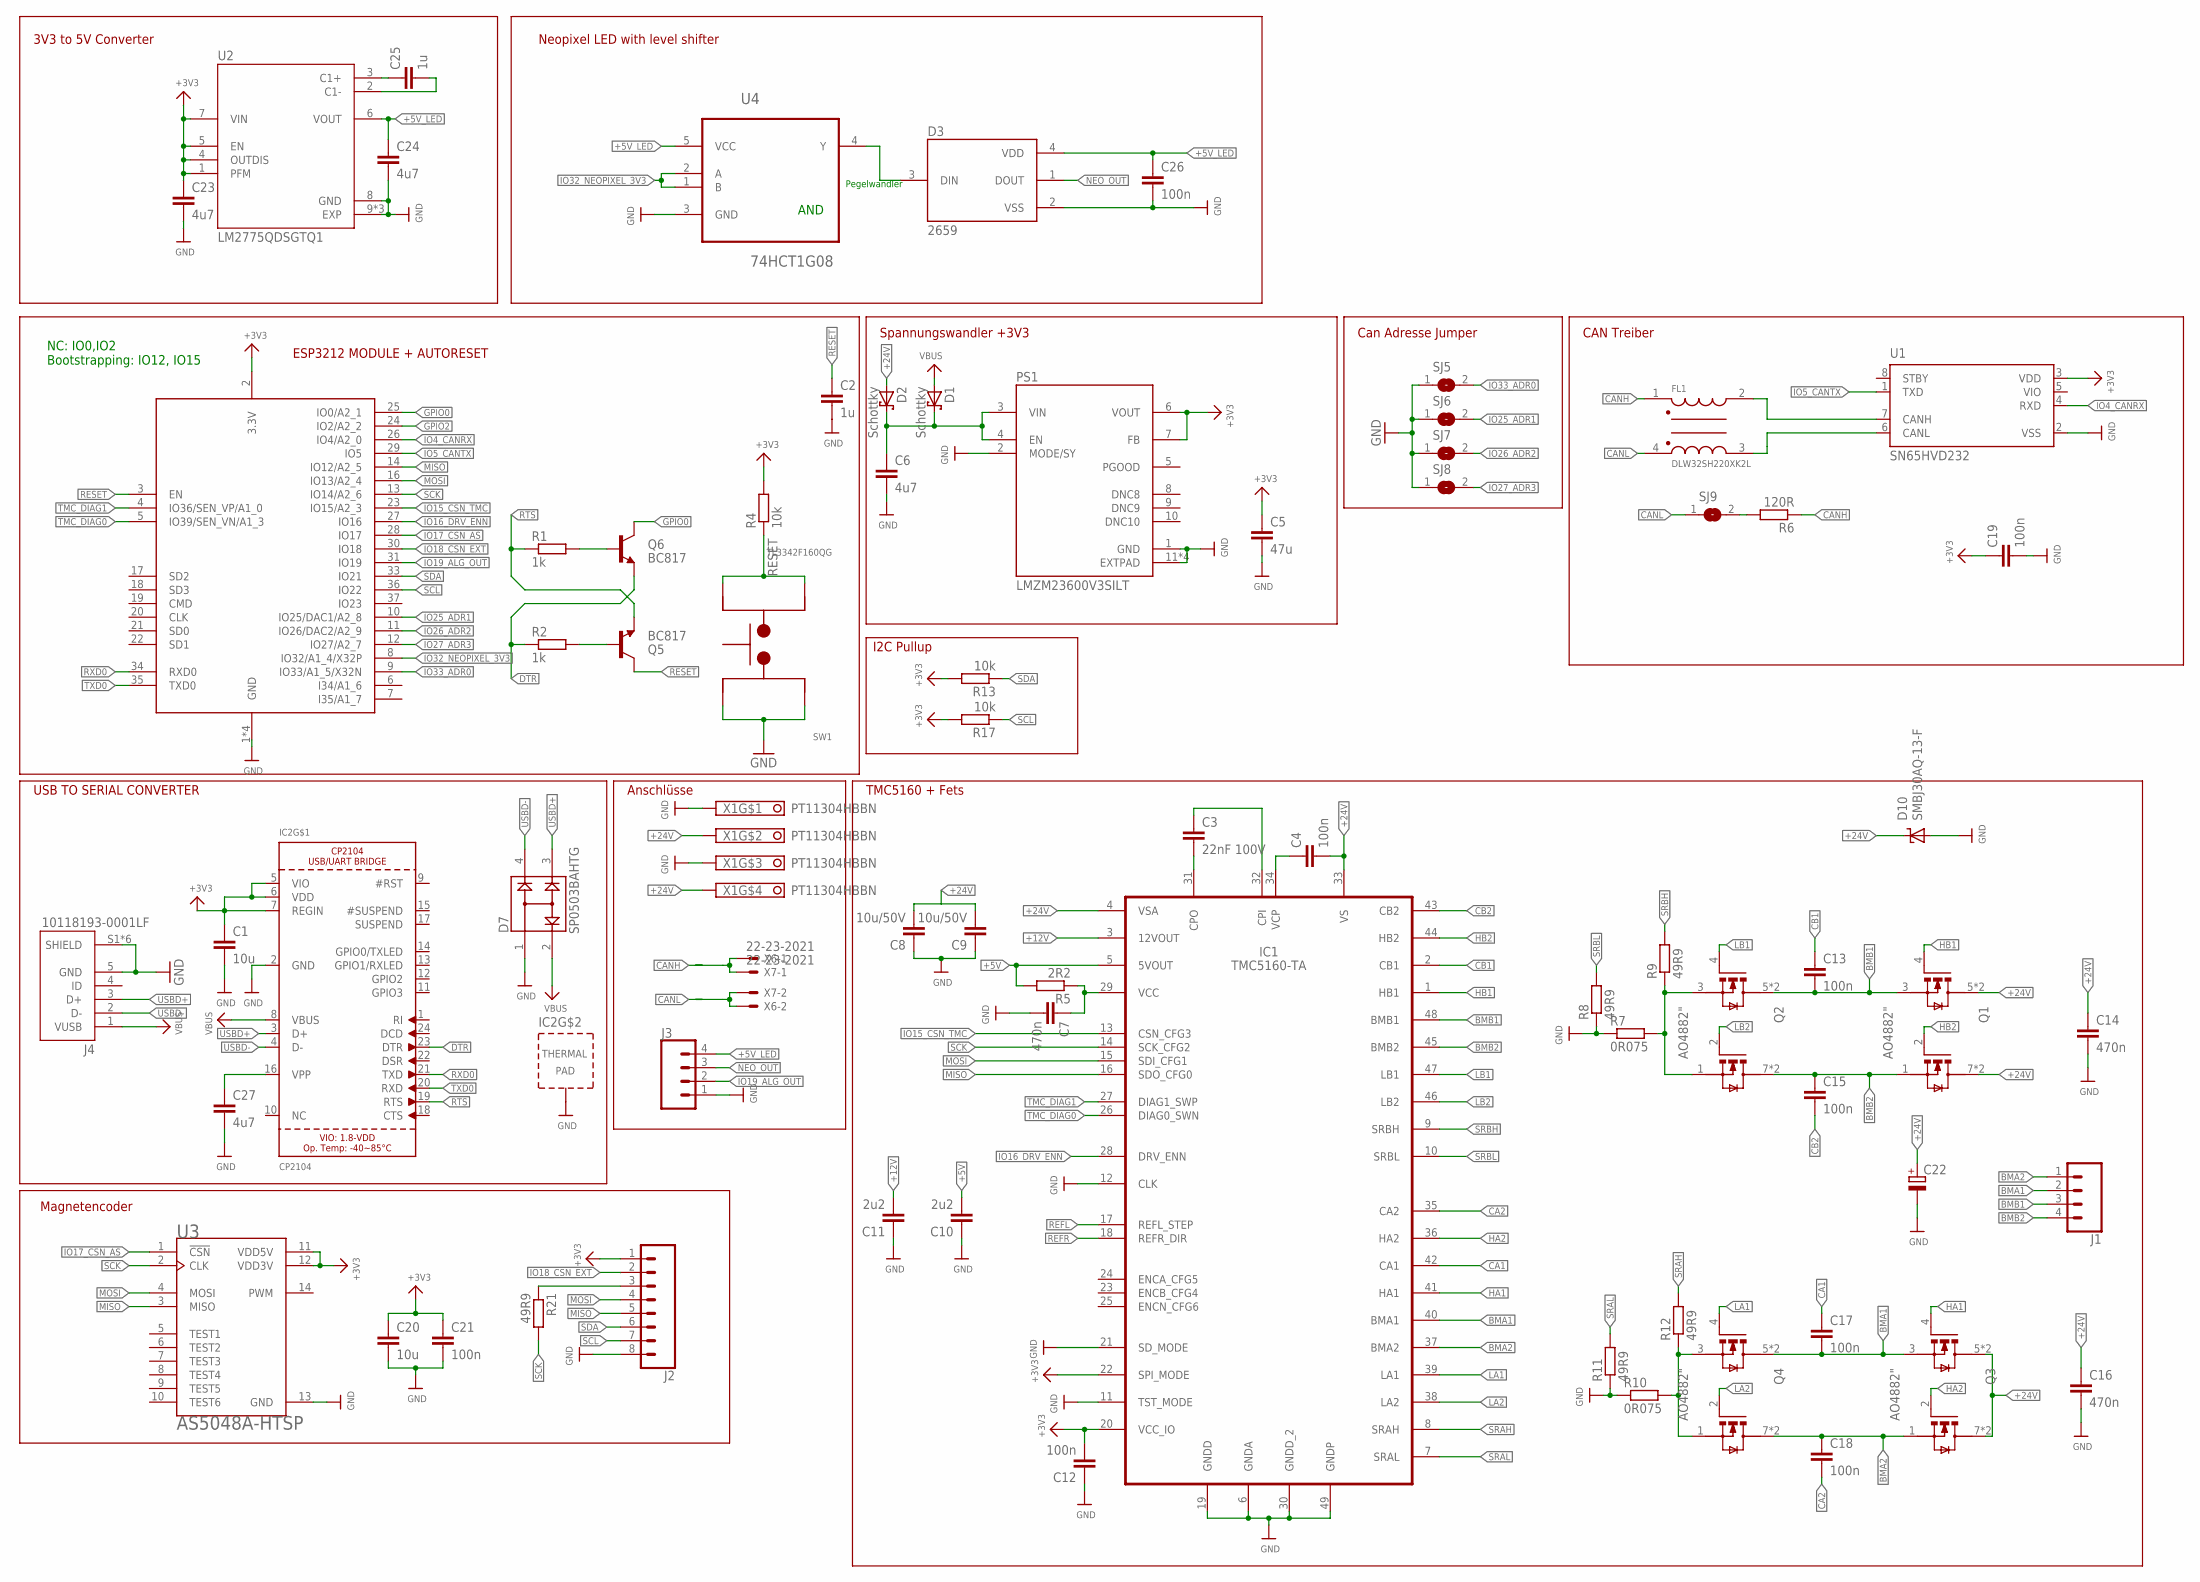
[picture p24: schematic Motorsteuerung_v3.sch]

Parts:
C1, C20: 10u; C0805
C2, C25: 1u; C0805
C3: 22nF 100V; C0805
C4, C12, C13, C15, C17, C18, C19, C21, C26: 100n; C0805
C5: 47u; C0805
C6, C23, C24, C27: 4u7; C0805
C7, C14, C16: 470n; C0805
C8, C9: 10u/50V; C0805
C10, C11: 2u2; C0805
C22: CPOL-EUE5-10.5; E5-10,5
D1, D2: Schottky; SMB
D3: 2659
D7: SP0503BAHTG; SOT143
D10: SMBJ30AQ-13-F; SMBJ
FL1: DLW32SH220XK2L; FIL_DLW32SH110XK2L
IC1: TMC5160-TA; TQFP48-EP
IC2: CP2104; QFN24_4MM_SMSC
J1: CONN_04; 1X04
J2: CONN_08BM08B-SRSS-TB; BM08B-SRSS-TB
J3: CONN_041.27MM; 1X04_1.27MM
J4: 10118193-0001LF; FCI_10118193-0001LF
PS1: LMZM23600V3SILT; CONV_LMZM23600V3SILT
Q1, Q2, Q3, Q4: AO4882"; SOIC8
Q5, Q6: BC817; SOT23-3
R1, R2: 1k; R0805
R4, R13, R17: 10k; R0805
R5: 2R2; R0805
R6: 120R; R0805
R7, R10: 0R075; R1206
R8, R9, R11, R12, R21: 49R9; R0805
SJ5, SJ6, SJ7, SJ8, SJ9: SJ
SW1: TL3342F160QG; SW_TL3342F160QG
U1: SN65HVD232; SOIC127P600X175-8N
U2: LM2775QDSGTQ1; SON50P200X200X80-9N
U3: AS5048A-HTSP; SOP65P640X120-14N
U4: 74HCT1G08; SOT65P210X110-5N
X1: PT11304HBBN; TYP184_FT
X2: ESP32_WROOM32_SKINNY; WROOM32_SKINNY
X6, X7: 22-23-2021

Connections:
+3V3: C1.1, C5.1, C12.2, C19.1, C20.1, C21.1, C23.1, IC1.20 (VCC_IO), IC1.22 (SPI_MODE), IC2.5 (VIO), IC2.6 (VDD), IC2.7 (REGIN), J2.1, PS1.6 (VOUT), PS1.7 (FB), R4.2, R13.2, R17.2, U1.3 (VDD), U2.1 (PFM), U2.4 (OUTDIS), U2.5 (EN), U2.7 (VIN), U3.11 (VDD5V), U3.12 (VDD3V), X2.2 (3.3V)
+5V: C10.2, IC1.5 (5VOUT), R5.2
+5V_LED: C24.1, C26.1, D3.4 (VDD), J3.4, U2.6 (VOUT), U4.5 (VCC)
+12V: C11.2, IC1.3 (12VOUT)
+24V: C4.2, C8.2, C9.2, C14.1, C16.1, C22.+, D2.A, D10.C, IC1.4 (VSA), IC1.33 (VS), Q1.5 (D1), Q1.6 (D1), Q1.7 (D2), Q1.8 (D2), Q3.5 (D1), Q3.6 (D1), Q3.7 (D2), Q3.8 (D2), X1.2, X1.4
BMA1: C17.2, IC1.40 (BMA1), J1.2, Q3.3 (S1), Q4.5 (D1), Q4.6 (D1)
BMA2: C18.1, IC1.37 (BMA2), J1.1, Q3.1 (S2), Q4.7 (D2), Q4.8 (D2)
BMB1: C13.2, IC1.48 (BMB1), J1.3, Q1.3 (S1), Q2.5 (D1), Q2.6 (D1)
BMB2: C15.1, IC1.45 (BMB2), J1.4, Q1.1 (S2), Q2.7 (D2), Q2.8 (D2)
CA1: C17.1, IC1.42 (CA1)
CA2: C18.2, IC1.35 (CA2)
CANH: FL1.1, R6.1, X6.1, X7.1
CANL: FL1.4, SJ9.1, X6.2, X7.2
CB1: C13.1, IC1.2 (CB1)
CB2: C15.2, IC1.43 (CB2)
DTR: IC2.23 (DTR), Q6.2 (E), R2.1
GND: C1.2, C2.2, C5.2, C6.2, C7.2, C8.1, C9.1, C10.1, C11.1, C12.1, C14.2, C16.2, C19.2, C20.2, C21.2, C22.-, C23.2, C24.2, C26.2, C27.2, D3.2 (VSS), D7.1, D10.A, IC1.6 (GNDA), IC1.11 (TST_MODE), IC1.12 (CLK), IC1.19 (GNDD), IC1.21 (SD_MODE), IC1.30 (GNDD_2), IC1.49 (GNDP), IC2.2 (GND), IC2.THERM (TP), J2.8, J3.1, J4.5 (GND), J4.S1 (SHIELD), J4.S2 (SHIELD), J4.S3 (SHIELD), J4.S4 (SHIELD), J4.S5 (SHIELD), J4.S6 (SHIELD), PS1.1 (GND), PS1.2 (MODE/SY), PS1.11 (EXTPAD), PS1.11_1 (EXTPAD), PS1.11_2 (EXTPAD), PS1.11_3 (EXTPAD), R7.1, R8.1, R10.1, R11.1, SJ5.1, SJ6.1, SJ7.1, SJ8.1, SW1.3, SW1.4, U1.2 (VSS), U2.8 (GND), U2.9 (EXP), U2.9_1 (EXP), U2.9_2 (EXP), U3.13 (GND), U4.3 (GND), X1.1, X1.3, X2.1 (GND), X2.15 (GND), X2.38 (GND), X2.P$1 (GND)
GPIO0: Q6.3 (C), X2.25 (IO0/A2_1)
GPIO2: X2.24 (IO2/A2_2)
HA1: IC1.41 (HA1), Q3.4 (G1)
HA2: IC1.36 (HA2), Q3.2 (G2)
HB1: IC1.1 (HB1), Q1.4 (G1)
HB2: IC1.44 (HB2), Q1.2 (G2)
IO4_CANRX: U1.4 (RXD), X2.26 (IO4/A2_0)
IO5_CANTX: U1.1 (TXD), X2.29 (IO5)
IO15_CSN_TMC: IC1.13 (CSN_CFG3), X2.23 (IO15/A2_3)
IO16_DRV_ENN: IC1.28 (DRV_ENN), X2.27 (IO16)
IO17_CSN_AS: U3.1 (!CSN), X2.28 (IO17)
IO18_CSN_EXT: J2.2, X2.30 (IO18)
IO19_ALG_OUT: J3.2, X2.31 (IO19)
IO25_ADR1: SJ6.2, X2.10 (IO25/DAC1/A2_8)
IO26_ADR2: SJ7.2, X2.11 (IO26/DAC2/A2_9)
IO27_ADR3: SJ8.2, X2.12 (IO27/A2_7)
IO32_NEOPIXEL_3V3: U4.1 (B), U4.2 (A), X2.8 (IO32/A1_4/X32P)
IO33_ADR0: SJ5.2, X2.9 (IO33/A1_5/X32N)
LA1: IC1.39 (LA1), Q4.4 (G1)
LA2: IC1.38 (LA2), Q4.2 (G2)
LB1: IC1.47 (LB1), Q2.4 (G1)
LB2: IC1.46 (LB2), Q2.2 (G2)
MISO: IC1.16 (SDO_CFG0), J2.5, U3.3 (MISO), X2.14 (IO12/A2_5)
MOSI: IC1.15 (SDI_CFG1), J2.4, U3.4 (MOSI), X2.16 (IO13/A2_4)
unnamed: C25.1, U2.3 (C1+)
unnamed: C6.1, D1.C, D2.C, PS1.3 (VIN), PS1.4 (EN)
unnamed: C3.2, IC1.31 (CPO)
unnamed: C3.1, IC1.32 (CPI)
unnamed: C4.1, IC1.34 (VCP)
unnamed: C25.2, U2.2 (C1-)
unnamed: C7.1, IC1.29 (VCC), R5.1
unnamed: FL1.2, U1.7 (CANH)
unnamed: Q4.1 (S2), Q4.3 (S1), R10.2, R12.1
unnamed: Q2.1 (S2), Q2.3 (S1), R7.2, R9.1
unnamed: FL1.3, U1.6 (CANL)
unnamed: Q5.1 (B), R2.2
unnamed: Q6.1 (B), R1.2
unnamed: D3.3 (DIN), U4.4 (Y)
unnamed: R6.2, SJ9.2
unnamed: J2.3, R21.1
unnamed: C27.1, IC2.16 (VPP)
NEO_OUT: D3.1 (DOUT), J3.3
REFL: IC1.17 (REFL_STEP)
REFR: IC1.18 (REFR_DIR)
RESET: C2.1, Q5.3 (C), R4.1, SW1.1, SW1.2, X2.3 (EN)
RTS: IC2.19 (RTS), Q5.2 (E), R1.1
RXD0: IC2.21 (TXD), X2.34 (RXD0)
SCK: IC1.14 (SCK_CFG2), R21.2, U3.2 (CLK), X2.13 (IO14/A2_6)
SCL: J2.7, R17.1, X2.36 (IO22)
SDA: J2.6, R13.1, X2.33 (IO21)
SRAH: IC1.8 (SRAH), R12.2
SRAL: IC1.7 (SRAL), R11.2
SRBH: IC1.9 (SRBH), R9.2
SRBL: IC1.10 (SRBL), R8.2
TMC_DIAG0: IC1.26 (DIAG0_SWN), X2.5 (IO39/SEN_VN/A1_3)
TMC_DIAG1: IC1.27 (DIAG1_SWP), X2.4 (IO36/SEN_VP/A1_0)
TXD0: IC2.20 (RXD), X2.35 (TXD0)
USBD+: D7.3, IC2.3 (D+), J4.3 (D+)
USBD-: D7.4, IC2.4 (D-), J4.2 (D-)
VBUS: D1.A, D7.2, IC2.8 (VBUS), J4.1 (VUSB)
VIO: U1.5 (VIO)

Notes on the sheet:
USB TO SERIAL CONVERTER
ESP3212 MODULE + AUTORESET
NC: IO0,IO2 Bootstrapping: IO12, IO15
Spannungswandler +3V3
CAN Treiber
Anschlüsse
TMC5160 + Fets
Magnetencoder
Can Adresse Jumper
I2C Pullup
Pegelwandler
AND
3V3 to 5V Converter
Neopixel LED with level shifter

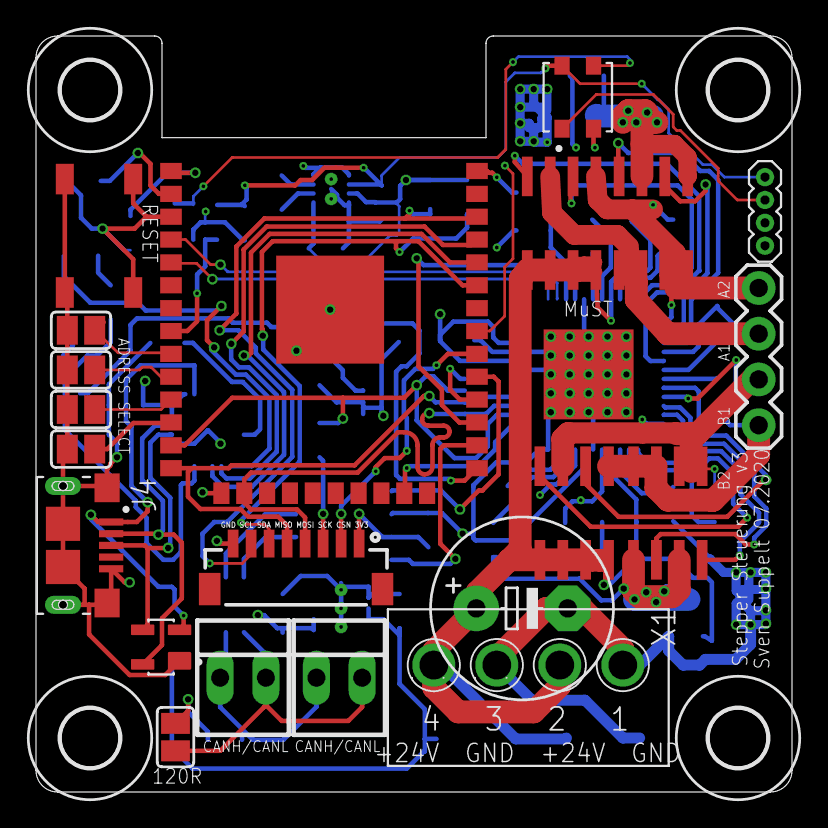
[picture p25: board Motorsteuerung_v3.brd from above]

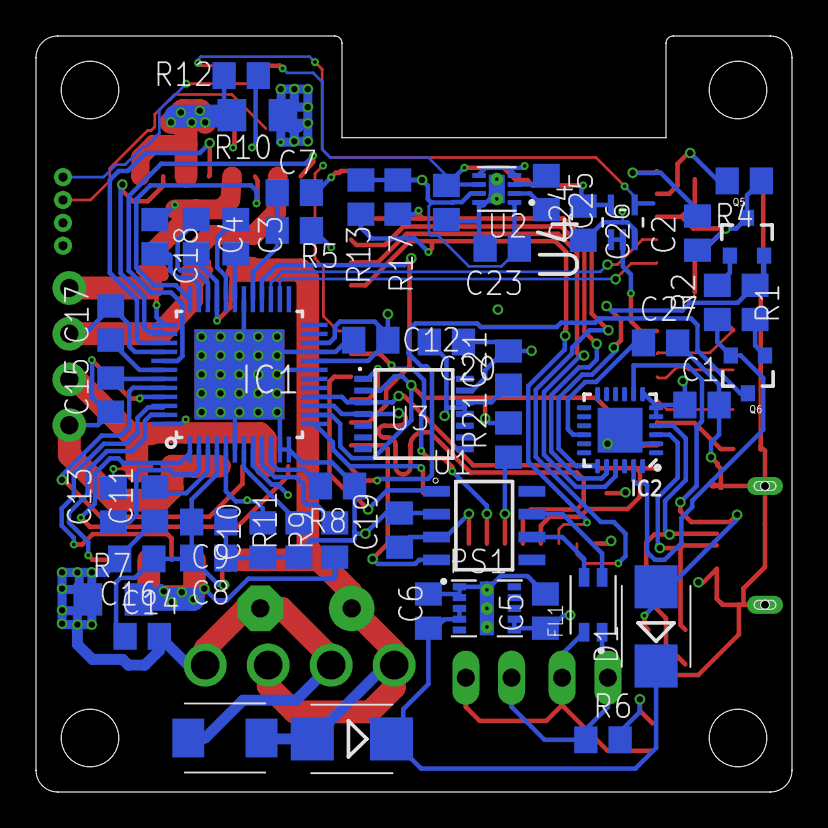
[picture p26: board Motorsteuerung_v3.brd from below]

Board: 4 copper layers, 42.0 x 42.0 mm, 78 parts (53 on the bottom side), 74 nets.

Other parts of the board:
U$1, U$2, U$3, U$4: 3,2

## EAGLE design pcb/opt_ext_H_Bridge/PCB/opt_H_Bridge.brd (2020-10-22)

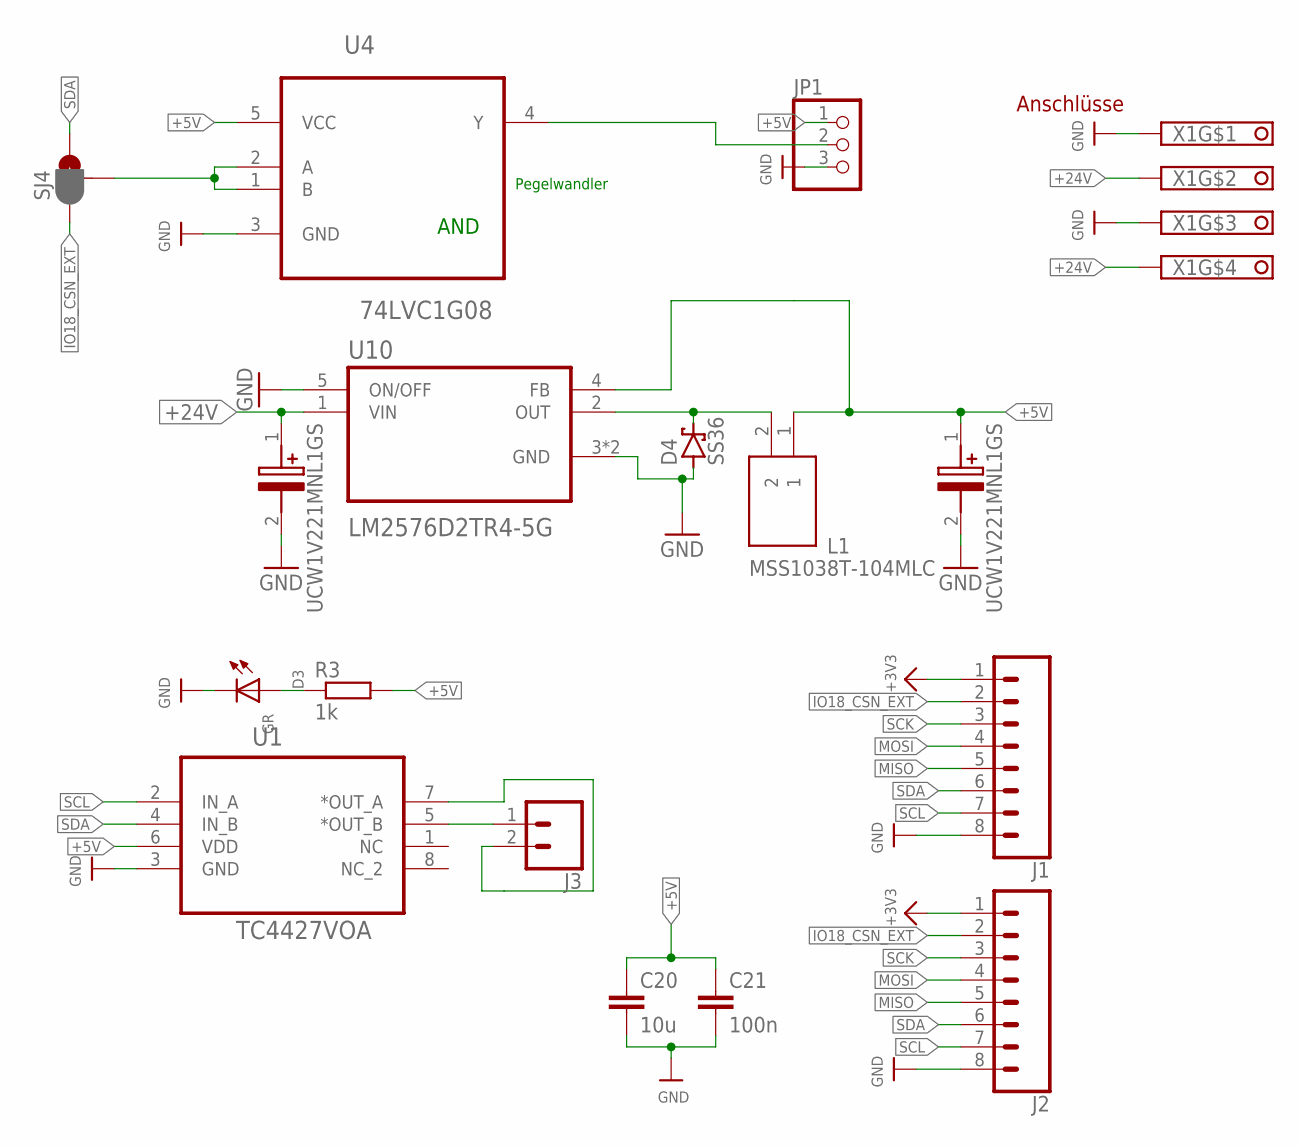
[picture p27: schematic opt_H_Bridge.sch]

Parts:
C1, C31: UCW1V221MNL1GS; UWT(8X10)
C20: 10u; C0805
C21: 100n; C0805
D3: GR; CHIP-LED0805
D4: SS36; SMC
J1, J2: CONN_08BM08B-SRSS-TB; BM08B-SRSS-TB
J3: CONN_023.5MM; SCREWTERMINAL-3.5MM-2
JP1: PINHD-1X3; 1X03
L1: MSS1038T-104MLC; INDPM102100X400N
R3: 1k; R0805
SJ4: JUMPER_PAD-3-1&2_NC_BY_PASTE; PAD-HUMPER-3-1&2_NC_BY_PASTE_YES_SILK_FULL_BOX
U1: TC4427VOA; SOIC127P600X175-8N
U4: 74LVC1G08; SOT65P210X110-5N
U10: LM2576D2TR4-5G; VREG_TPS79625KTTR
X1: PT11304HBBN; TYP184_FT

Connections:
+3V3: J1.1, J2.1
+5V: C1.1 (+), C20.1, C21.1, JP1.1, L1.1, R3.2, U1.6 (VDD), U4.5 (VCC), U10.4 (FB)
+24V: C31.1 (+), U10.1 (VIN), X1.2, X1.4
GND: C1.2 (-), C20.2, C21.2, C31.2 (-), D3.C, D4.A, J1.8, J2.8, JP1.3, U1.3 (GND), U4.3 (GND), U10.3 (GND), U10.5 (ON/OFF), U10.6 (GND), X1.1, X1.3
IO18_CSN_EXT: J1.2, J2.2, SJ4.1
MISO: J1.5, J2.5
MOSI: J1.4, J2.4
unnamed: J3.1, U1.5 (*OUT_B)
unnamed: J3.2, U1.7 (*OUT_A)
unnamed: JP1.2, U4.4 (Y)
unnamed: SJ4.2, U4.1 (B), U4.2 (A)
unnamed: D3.A, R3.1
unnamed: D4.C, L1.2, U10.2 (OUT)
SCK: J1.3, J2.3
SCL: J1.7, J2.7, U1.2 (IN_A)
SDA: J1.6, J2.6, SJ4.3, U1.4 (IN_B)

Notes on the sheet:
Anschlüsse
Pegelwandler
AND

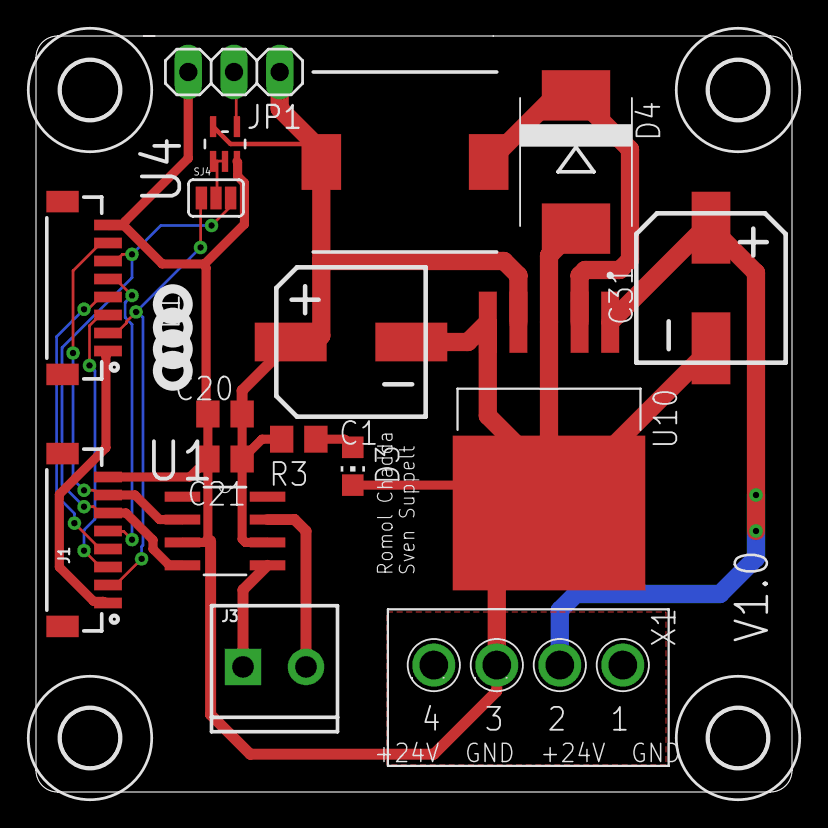
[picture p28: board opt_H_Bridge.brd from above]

Board: 2 copper layers, 42.0 x 42.0 mm, 21 parts (0 on the bottom side), 16 nets.

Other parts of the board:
U$1, U$2, U$3, U$4: 3,2

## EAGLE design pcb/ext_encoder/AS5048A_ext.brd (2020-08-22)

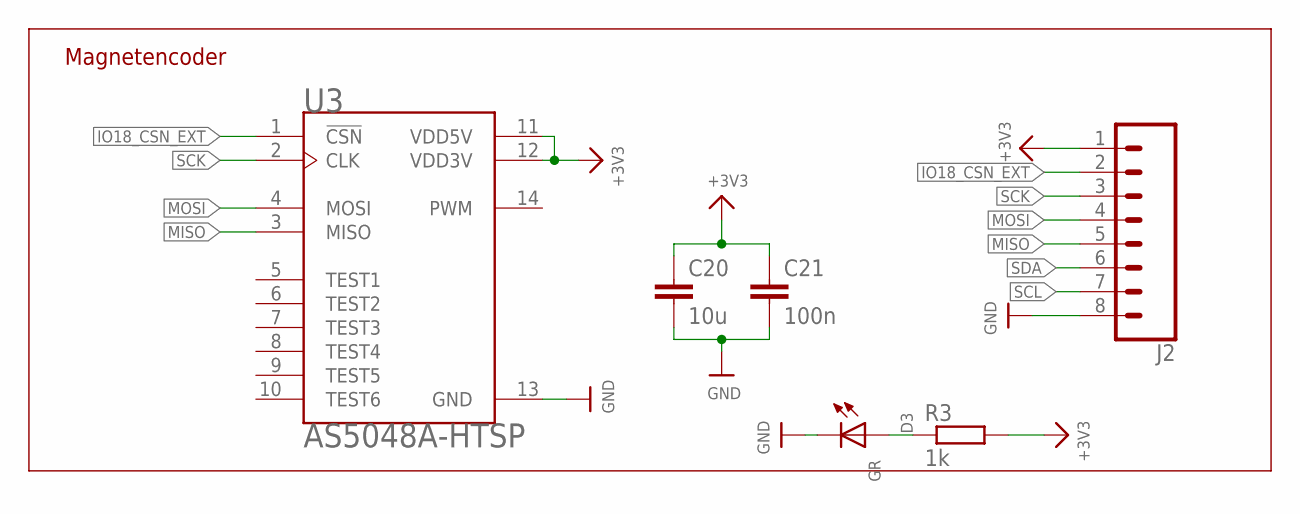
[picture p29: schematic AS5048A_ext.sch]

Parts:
C20: 10u; C0805
C21: 100n; C0805
D3: GR; CHIP-LED0805
J2: CONN_08BM08B-SRSS-TB; BM08B-SRSS-TB
R3: 1k; R0805
U3: AS5048A-HTSP; SOP65P640X120-14N

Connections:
+3V3: C20.1, C21.1, J2.1, R3.2, U3.11 (VDD5V), U3.12 (VDD3V)
GND: C20.2, C21.2, D3.C, J2.8, U3.13 (GND)
IO18_CSN_EXT: J2.2, U3.1 (!CSN)
MISO: J2.5, U3.3 (MISO)
MOSI: J2.4, U3.4 (MOSI)
unnamed: D3.A, R3.1
SCK: J2.3, U3.2 (CLK)
SCL: J2.7
SDA: J2.6

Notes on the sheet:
Magnetencoder

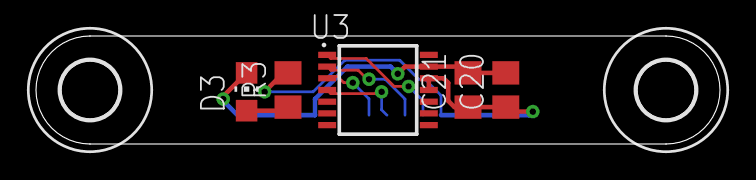
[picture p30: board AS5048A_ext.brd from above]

Board: 2 copper layers, 38.0 x 6.0 mm, 8 parts (1 on the bottom side), 7 nets.

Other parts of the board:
U$1, U$2: 3,2

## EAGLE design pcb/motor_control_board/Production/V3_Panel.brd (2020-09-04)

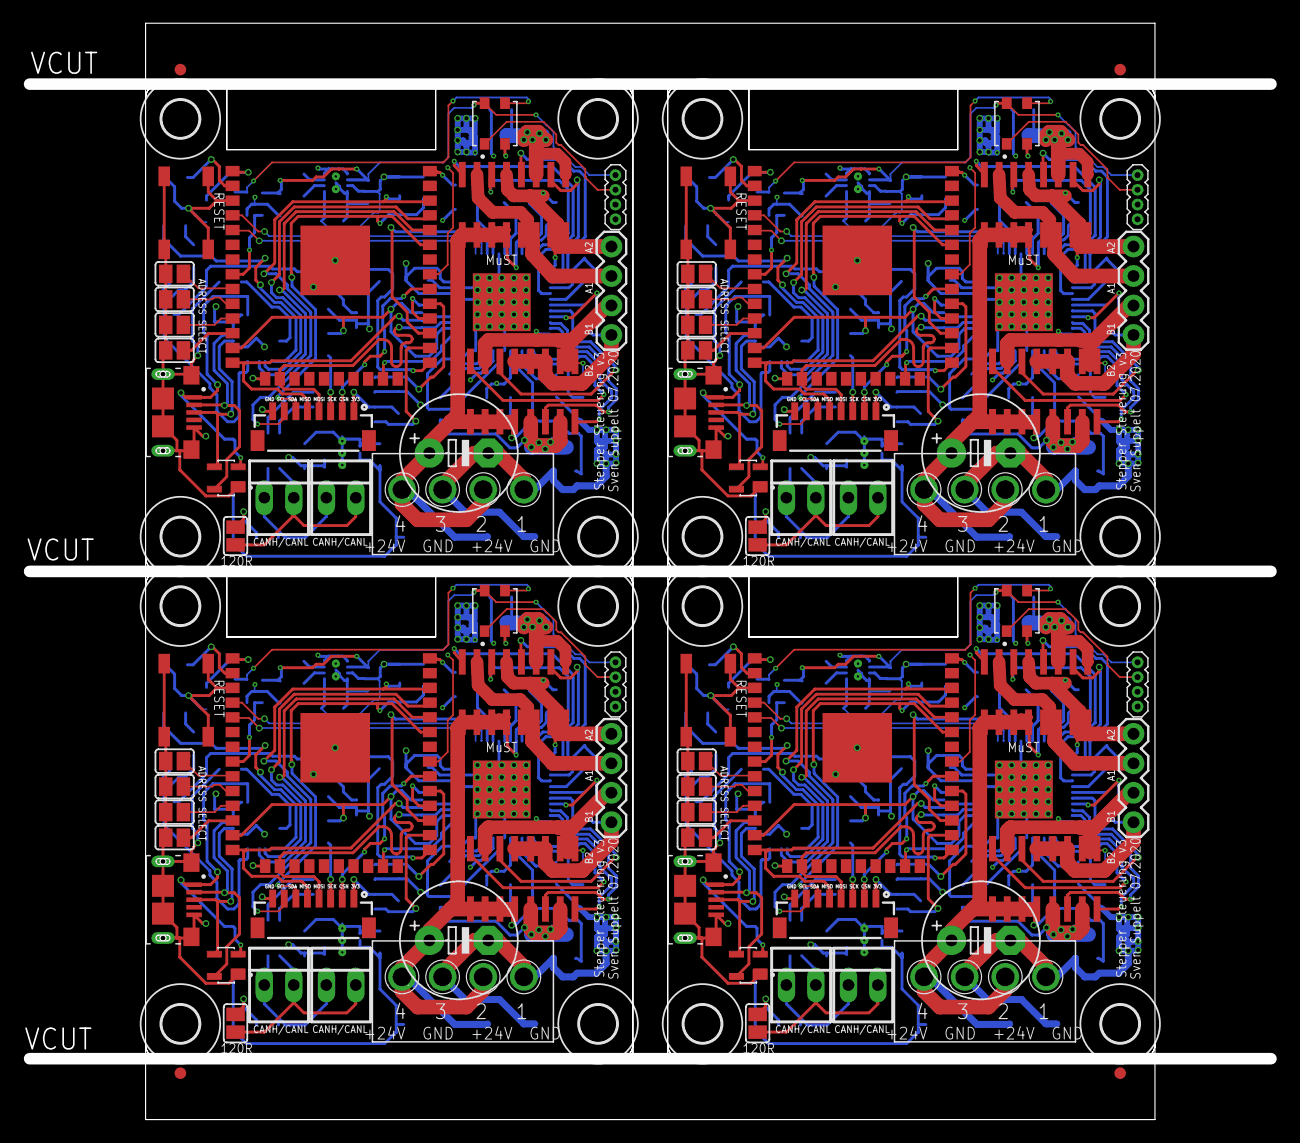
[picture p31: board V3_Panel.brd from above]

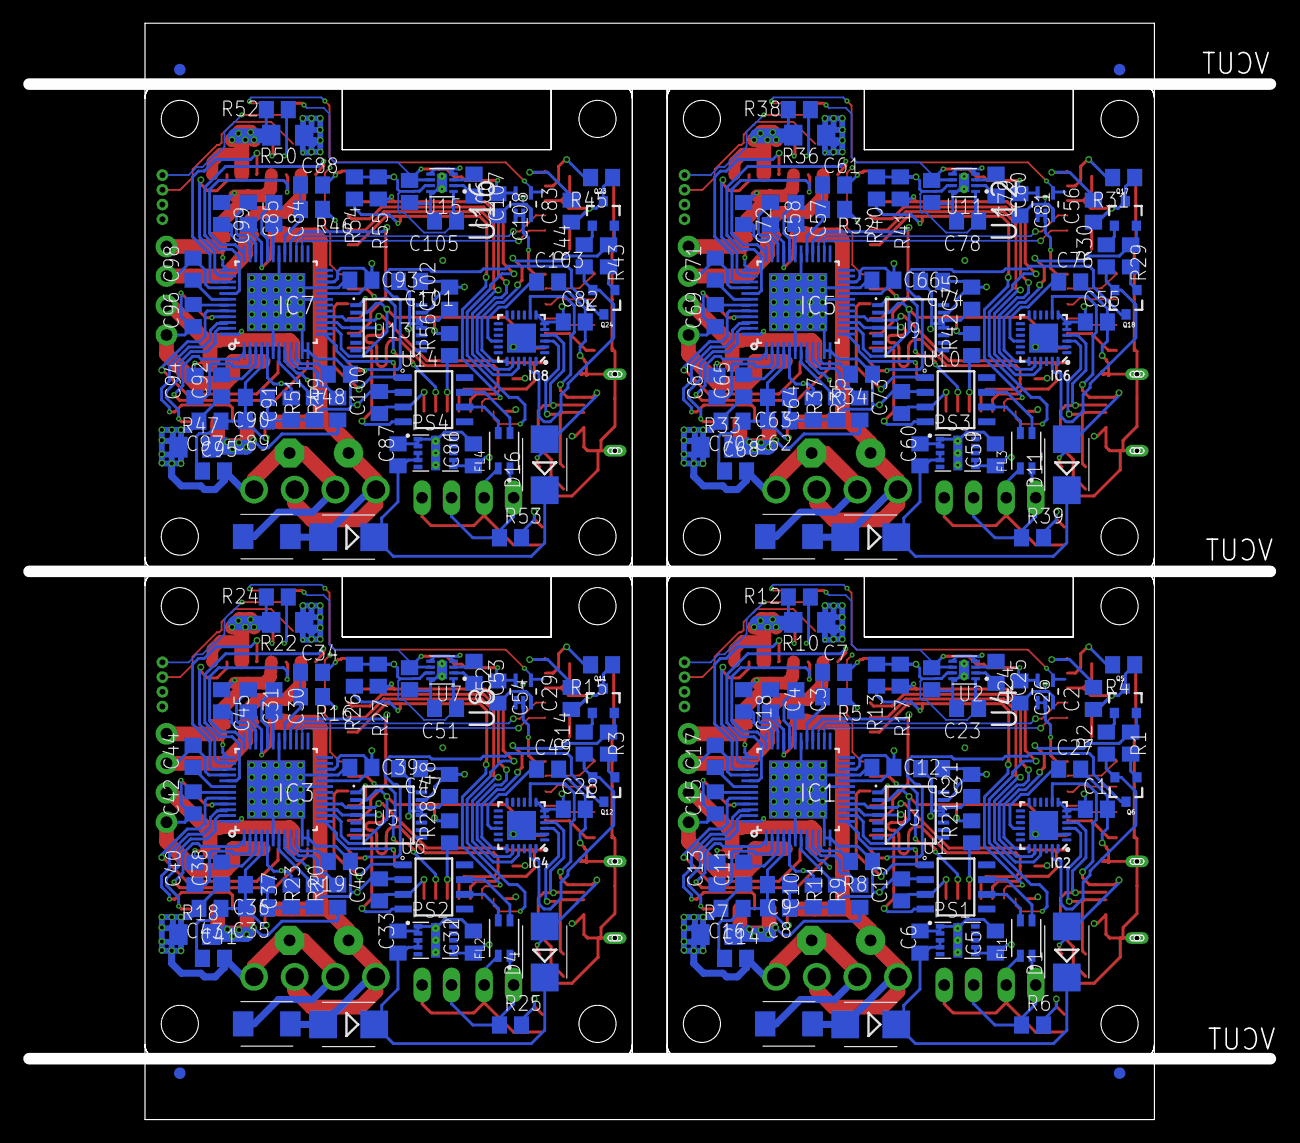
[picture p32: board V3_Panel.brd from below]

Board: 4 copper layers, 87.0 x 94.5 mm, 320 parts (216 on the bottom side), 296 nets.

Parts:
C1, C20, C28, C47, C55, C74, C82, C101: 10u; C0805
C2, C25, C29, C53, C56, C80, C83, C107: 1u; C0805
C3, C30, C57, C84: 22nF 100V; C0805
C4, C12, C13, C15, C17, C18, C19, C21, C26, C31, C39, C40, C42, C44, C45, C46, C48, C54, C58, C66, C67, C69, C71, C72, C73, C75, C81, C85, C93, C94, C96, C98, C99, C100, C102, C108: 100n; C0805
C5, C32, C59, C86: 47u; C0805
C6, C23, C24, C27, C33, C49, C51, C52, C60, C76, C78, C79, C87, C103, C105, C106: 4u7; C0805
C7, C14, C16, C34, C41, C43, C61, C68, C70, C88, C95, C97: 470n; C0805
C8, C9, C35, C36, C62, C63, C89, C90: 10u/50V; C0805
C10, C11, C37, C38, C64, C65, C91, C92: 2u2; C0805
C22, C50, C77, C104: E5-10,5
D1, D2, D4, D5, D11, D12, D16, D17: Schottky; SMB
D3, D9, D15, D20: 2659
D6, D7, D13, D18: SP0503BAHTG; SOT143
D8, D10, D14, D19: SMBJ30AQ-13-F; SMBJ
E$1, E$2, E$3, E$4, E$5, E$6, E$7, E$8: FIDUCIAL_1MM
FL1, FL2, FL3, FL4: DLW32SH220XK2L; FIL_DLW32SH110XK2L
IC1, IC3, IC5, IC7: TMC5160-TA; TQFP48-EP
IC2, IC4, IC6, IC8: CP2104; QFN24_4MM_SMSC
J1, J5, J9, J13: 1X04
J2, J6, J10, J14: BM08B-SRSS-TB
J3, J7, J11, J15: 1X04_1.27MM
J4, J8, J12, J16: 10118193-0001LF; FCI_10118193-0001LF
PS1, PS2, PS3, PS4: LMZM23600V3SILT; CONV_LMZM23600V3SILT
Q1, Q2, Q3, Q4, Q7, Q8, Q9, Q10, Q13, Q14, Q15, Q16, Q19, Q20, Q21, Q22: AO4882"; SOIC8
Q5, Q6, Q11, Q12, Q17, Q18, Q23, Q24: BC817; SOT23-3
R1, R2, R3, R14, R29, R30, R43, R44: 1k; R0805
R4, R13, R15, R17, R26, R27, R31, R40, R41, R45, R54, R55: 10k; R0805
R5, R16, R32, R46: 2R2; R0805
R6, R25, R39, R53: 120R; R0805
R7, R10, R18, R22, R33, R36, R47, R50: 0R075; R1206
R8, R9, R11, R12, R19, R20, R21, R23, R24, R28, R34, R35, R37, R38, R42, R48, R49, R51, R52, R56: 49R9; R0805
SJ1, SJ2, SJ3, SJ4, SJ5, SJ6, SJ7, SJ8, SJ9, SJ10, SJ11, SJ12, SJ13, SJ14, SJ15, SJ16, SJ17, SJ18, SJ19, SJ20: SJ
SW1, SW2, SW3, SW4: TL3342F160QG; SW_TL3342F160QG
U1, U6, U10, U14: SN65HVD232; SOIC127P600X175-8N
U2, U7, U11, U15: LM2775QDSGTQ1; SON50P200X200X80-9N
U3, U5, U9, U13: AS5048A-HTSP; SOP65P640X120-14N
U4, U8, U12, U16: 74LVC1G08; SOT65P210X110-5N
U$1, U$2, U$3, U$4, U$5, U$6, U$7, U$8, U$9, U$10, U$11, U$12, U$13, U$14, U$15, U$16: 3,2
X1, X8, X12, X16: PT11304HBBN; TYP184_FT
X2, X3, X9, X13: ESP32_WROOM32_SKINNY; WROOM32_SKINNY
X4, X5, X6, X7, X10, X11, X14, X15: 22-23-2021

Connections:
+3V1: C28.1, C32.1, C39.2, C46.1, C47.1, C48.1, C51.1, IC3.20, IC3.22, IC4.5, IC4.6, IC4.7, J6.1, PS2.6, PS2.7, R15.2, R26.2, R27.2, U5.11, U5.12, U6.3, U7.1, U7.4, U7.5, U7.7, X3.2
+3V2: C55.1, C59.1, C66.2, C73.1, C74.1, C75.1, C78.1, IC5.20, IC5.22, IC6.5, IC6.6, IC6.7, J10.1, PS3.6, PS3.7, R31.2, R40.2, R41.2, U9.11, U9.12, U10.3, U11.1, U11.4, U11.5, U11.7, X9.2
+3V3: C1.1, C5.1, C12.2, C19.1, C20.1, C21.1, C23.1, IC1.20, IC1.22, IC2.5, IC2.6, IC2.7, J2.1, PS1.6, PS1.7, R4.2, R13.2, R17.2, U1.3, U2.1, U2.4, U2.5, U2.7, U3.11, U3.12, X2.2
+3V4: C82.1, C86.1, C93.2, C100.1, C101.1, C102.1, C105.1, IC7.20, IC7.22, IC8.5, IC8.6, IC8.7, J14.1, PS4.6, PS4.7, R45.2, R54.2, R55.2, U13.11, U13.12, U14.3, U15.1, U15.4, U15.5, U15.7, X13.2
+5V: C10.2, IC1.5, R5.2
+5V1: C37.2, IC3.5, R16.2
+5V2: C64.2, IC5.5, R32.2
+5V3: C91.2, IC7.5, R46.2
+5V_LED: C24.1, C26.1, D3.4, J3.4, U2.6, U4.5
+5V_LED1: C52.1, C54.1, D9.4, J7.4, U7.6, U8.5
+5V_LED2: C79.1, C81.1, D15.4, J11.4, U11.6, U12.5
+5V_LED3: C106.1, C108.1, D20.4, J15.4, U15.6, U16.5
+12V: C11.2, IC1.3
+12V1: C38.2, IC3.3
+12V2: C65.2, IC5.3
+12V3: C92.2, IC7.3
+24V: C4.2, C8.2, C9.2, C14.1, C16.1, C22.+, D2.A, D10.C, IC1.4, IC1.33, Q1.5, Q1.6, Q1.7, Q1.8, Q3.5, Q3.6, Q3.7, Q3.8, X1.2, X1.4
+24V1: C31.2, C35.2, C36.2, C41.1, C43.1, C50.+, D5.A, D8.C, IC3.4, IC3.33, Q7.5, Q7.6, Q7.7, Q7.8, Q9.5, Q9.6, Q9.7, Q9.8, X8.2, X8.4
+24V2: C58.2, C62.2, C63.2, C68.1, C70.1, C77.+, D12.A, D14.C, IC5.4, IC5.33, Q13.5, Q13.6, Q13.7, Q13.8, Q15.5, Q15.6, Q15.7, Q15.8, X12.2, X12.4
+24V3: C85.2, C89.2, C90.2, C95.1, C97.1, C104.+, D17.A, D19.C, IC7.4, IC7.33, Q19.5, Q19.6, Q19.7, Q19.8, Q21.5, Q21.6, Q21.7, Q21.8, X16.2, X16.4
BMA1: C17.2, IC1.40, J1.2, Q3.3, Q4.5, Q4.6
BMA2: C18.1, IC1.37, J1.1, Q3.1, Q4.7, Q4.8
BMA3: C45.1, IC3.37, J5.1, Q9.1, Q10.7, Q10.8
BMA4: C44.2, IC3.40, J5.2, Q9.3, Q10.5, Q10.6
BMA5: C72.1, IC5.37, J9.1, Q15.1, Q16.7, Q16.8
BMA6: C71.2, IC5.40, J9.2, Q15.3, Q16.5, Q16.6
BMA7: C99.1, IC7.37, J13.1, Q21.1, Q22.7, Q22.8
BMA8: C98.2, IC7.40, J13.2, Q21.3, Q22.5, Q22.6
BMB1: C13.2, IC1.48, J1.3, Q1.3, Q2.5, Q2.6
BMB2: C15.1, IC1.45, J1.4, Q1.1, Q2.7, Q2.8
BMB3: C40.2, IC3.48, J5.3, Q7.3, Q8.5, Q8.6
BMB4: C42.1, IC3.45, J5.4, Q7.1, Q8.7, Q8.8
BMB5: C67.2, IC5.48, J9.3, Q13.3, Q14.5, Q14.6
BMB6: C69.1, IC5.45, J9.4, Q13.1, Q14.7, Q14.8
BMB7: C94.2, IC7.48, J13.3, Q19.3, Q20.5, Q20.6
BMB8: C96.1, IC7.45, J13.4, Q19.1, Q20.7, Q20.8
CA1: C17.1, IC1.42
CA2: C18.2, IC1.35
CA3: C44.1, IC3.42
CA4: C45.2, IC3.35
CA5: C71.1, IC5.42
CA6: C72.2, IC5.35
CA7: C98.1, IC7.42
CA8: C99.2, IC7.35
CANH: FL1.1, R6.1, X6.1, X7.1
CANH1: FL2.1, R25.1, X4.1, X5.1
CANH2: FL3.1, R39.1, X10.1, X11.1
CANH3: FL4.1, R53.1, X14.1, X15.1
CANL: FL1.4, SJ9.1, X6.2, X7.2
CANL1: FL2.4, SJ10.1, X4.2, X5.2
CANL2: FL3.4, SJ15.1, X10.2, X11.2
CANL3: FL4.4, SJ20.1, X14.2, X15.2
CB1: C13.1, IC1.2
CB2: C15.2, IC1.43
CB3: C42.2, IC3.43
CB4: C40.1, IC3.2
CB5: C69.2, IC5.43
CB6: C67.1, IC5.2
CB7: C96.2, IC7.43
CB8: C94.1, IC7.2
DTR: IC2.23, Q6.2, R2.1
DTR1: IC4.23, Q12.2, R14.1
DTR2: IC6.23, Q18.2, R30.1
DTR3: IC8.23, Q24.2, R44.1
GND: C1.2, C2.2, C5.2, C6.2, C7.2, C8.1, C9.1, C10.1, C11.1, C12.1, C14.2, C16.2, C19.2, C20.2, C21.2, C22.-, C23.2, C24.2, C26.2, C27.2, D3.2, D7.1, D10.A, IC1.6, IC1.11, IC1.12, IC1.19, IC1.21, IC1.30, IC1.49, IC2.2, IC2.THERM, J2.8, J3.1, J4.5, J4.S1, J4.S2, J4.S3, J4.S4, J4.S5, J4.S6, PS1.1, PS1.2, PS1.11, PS1.11_1, PS1.11_2, PS1.11_3, R7.1, R8.1, R10.1, R11.1, SJ5.1, SJ6.1, SJ7.1, SJ8.1, SW1.3, SW1.4, U1.2, U2.8, U2.9, U2.9_1, U2.9_2, U3.13, U4.3, X1.1, X1.3, X2.1, X2.15, X2.38, X2.P$1
GND1: C28.2, C29.2, C32.2, C33.2, C34.2, C35.1, C36.1, C37.1, C38.1, C39.1, C41.2, C43.2, C46.2, C47.2, C48.2, C49.2, C50.-, C51.2, C52.2, C54.2, D6.1, D8.A, D9.2, IC3.6, IC3.11, IC3.12, IC3.19, IC3.21, IC3.30, IC3.49, IC4.2, IC4.THERM, J6.8, J7.1, J8.5, J8.S1, J8.S2, J8.S3, J8.S4, J8.S5, J8.S6, PS2.1, PS2.2, PS2.11, PS2.11_1, PS2.11_2, PS2.11_3, R18.1, R19.1, R22.1, R23.1, SJ1.1, SJ2.1, SJ3.1, SJ4.1, SW2.3, SW2.4, U5.13, U6.2, U7.8, U7.9, U7.9_1, U7.9_2, U8.3, X3.1, X3.15, X3.38, X3.P$1, X8.1, X8.3
GND2: C55.2, C56.2, C59.2, C60.2, C61.2, C62.1, C63.1, C64.1, C65.1, C66.1, C68.2, C70.2, C73.2, C74.2, C75.2, C76.2, C77.-, C78.2, C79.2, C81.2, D13.1, D14.A, D15.2, IC5.6, IC5.11, IC5.12, IC5.19, IC5.21, IC5.30, IC5.49, IC6.2, IC6.THERM, J10.8, J11.1, J12.5, J12.S1, J12.S2, J12.S3, J12.S4, J12.S5, J12.S6, PS3.1, PS3.2, PS3.11, PS3.11_1, PS3.11_2, PS3.11_3, R33.1, R34.1, R36.1, R37.1, SJ11.1, SJ12.1, SJ13.1, SJ14.1, SW3.3, SW3.4, U9.13, U10.2, U11.8, U11.9, U11.9_1, U11.9_2, U12.3, X9.1, X9.15, X9.38, X9.P$1, X12.1, X12.3
GND3: C82.2, C83.2, C86.2, C87.2, C88.2, C89.1, C90.1, C91.1, C92.1, C93.1, C95.2, C97.2, C100.2, C101.2, C102.2, C103.2, C104.-, C105.2, C106.2, C108.2, D18.1, D19.A, D20.2, IC7.6, IC7.11, IC7.12, IC7.19, IC7.21, IC7.30, IC7.49, IC8.2, IC8.THERM, J14.8, J15.1, J16.5, J16.S1, J16.S2, J16.S3, J16.S4, J16.S5, J16.S6, PS4.1, PS4.2, PS4.11, PS4.11_1, PS4.11_2, PS4.11_3, R47.1, R48.1, R50.1, R51.1, SJ16.1, SJ17.1, SJ18.1, SJ19.1, SW4.3, SW4.4, U13.13, U14.2, U15.8, U15.9, U15.9_1, U15.9_2, U16.3, X13.1, X13.15, X13.38, X13.P$1, X16.1, X16.3
GPIO0: Q6.3, X2.25
GPIO1: Q12.3, X3.25
GPIO4: Q18.3, X9.25
GPIO6: Q24.3, X13.25
HA1: IC1.41, Q3.4
HA2: IC1.36, Q3.2
HA3: IC3.41, Q9.4
HA4: IC3.36, Q9.2
HA5: IC5.41, Q15.4
HA6: IC5.36, Q15.2
HA7: IC7.41, Q21.4
HA8: IC7.36, Q21.2
HB1: IC1.1, Q1.4
HB2: IC1.44, Q1.2
HB3: IC3.44, Q7.2
HB4: IC3.1, Q7.4
HB5: IC5.44, Q13.2
HB6: IC5.1, Q13.4
HB7: IC7.44, Q19.2
HB8: IC7.1, Q19.4
IO4_CANRX: U1.4, X2.26
IO4_CANRX1: U6.4, X3.26
IO4_CANRX2: U10.4, X9.26
IO4_CANRX3: U14.4, X13.26
IO5_CANTX: U1.1, X2.29
IO5_CANTX1: U6.1, X3.29
IO5_CANTX2: U10.1, X9.29
IO5_CANTX3: U14.1, X13.29
IO15_CSN_TMC: IC1.13, X2.23
IO15_CSN_TMC1: IC3.13, X3.23
IO15_CSN_TMC2: IC5.13, X9.23
IO15_CSN_TMC3: IC7.13, X13.23
IO16_DRV_ENN: IC1.28, X2.27
IO16_DRV_ENN1: IC3.28, X3.27
IO16_DRV_ENN2: IC5.28, X9.27
IO16_DRV_ENN3: IC7.28, X13.27
IO17_CSN_AS: U3.1, X2.28
IO17_CSN_AS1: U5.1, X3.28
IO17_CSN_AS2: U9.1, X9.28
IO17_CSN_AS3: U13.1, X13.28
IO18_CSN_EXT: J2.2, X2.30
IO18_CSN_EXT1: J6.2, X3.30
IO18_CSN_EXT2: J10.2, X9.30
IO18_CSN_EXT3: J14.2, X13.30
IO19_ALG_OUT: J3.2, X2.31
IO19_ALG_OUT1: J7.2, X3.31
IO19_ALG_OUT2: J11.2, X9.31
IO19_ALG_OUT3: J15.2, X13.31
IO25_ADR1: SJ6.2, X2.10
IO25_ADR2: SJ2.2, X3.10
IO25_ADR3: SJ12.2, X9.10
IO25_ADR4: SJ17.2, X13.10
IO26_ADR1: SJ3.2, X3.11
IO26_ADR2: SJ7.2, X2.11
IO26_ADR3: SJ13.2, X9.11
IO26_ADR4: SJ18.2, X13.11
IO27_ADR1: SJ4.2, X3.12
IO27_ADR2: SJ14.2, X9.12
IO27_ADR3: SJ8.2, X2.12
IO27_ADR4: SJ19.2, X13.12
IO32_NEOPIXEL_3V1: U8.1, U8.2, X3.8
IO32_NEOPIXEL_3V2: U12.1, U12.2, X9.8
IO32_NEOPIXEL_3V3: U4.1, U4.2, X2.8
IO32_NEOPIXEL_3V4: U16.1, U16.2, X13.8
IO33_ADR0: SJ5.2, X2.9
IO33_ADR1: SJ1.2, X3.9
IO33_ADR2: SJ11.2, X9.9
IO33_ADR3: SJ16.2, X13.9
LA1: IC1.39, Q4.4
LA2: IC1.38, Q4.2
LA3: IC3.38, Q10.2
LA4: IC3.39, Q10.4
LA5: IC5.38, Q16.2
LA6: IC5.39, Q16.4
LA7: IC7.38, Q22.2
LA8: IC7.39, Q22.4
LB1: IC1.47, Q2.4
LB2: IC1.46, Q2.2
LB3: IC3.47, Q8.4
LB4: IC3.46, Q8.2
LB5: IC5.47, Q14.4
LB6: IC5.46, Q14.2
LB7: IC7.47, Q20.4
LB8: IC7.46, Q20.2
MISO: IC1.16, J2.5, U3.3, X2.14
MISO1: IC3.16, J6.5, U5.3, X3.14
MISO2: IC5.16, J10.5, U9.3, X9.14
MISO3: IC7.16, J14.5, U13.3, X13.14
MOSI: IC1.15, J2.4, U3.4, X2.16
MOSI1: IC3.15, J6.4, U5.4, X3.16
MOSI2: IC5.15, J10.4, U9.4, X9.16
MOSI3: IC7.15, J14.4, U13.4, X13.16
unnamed: C25.1, U2.3
unnamed: C6.1, D1.C, D2.C, PS1.3, PS1.4
unnamed: C3.2, IC1.31
unnamed: C3.1, IC1.32
unnamed: C4.1, IC1.34
unnamed: C25.2, U2.2
unnamed: C7.1, IC1.29, R5.1
unnamed: FL1.2, U1.7
unnamed: Q4.1, Q4.3, R10.2, R12.1
unnamed: Q2.1, Q2.3, R7.2, R9.1
unnamed: FL1.3, U1.6
unnamed: Q5.1, R2.2
unnamed: Q6.1, R1.2
unnamed: Q11.1, R14.2
unnamed: D3.3, U4.4
unnamed: R6.2, SJ9.2
unnamed: Q12.1, R3.2
unnamed: C30.2, IC3.31
unnamed: C30.1, IC3.32
unnamed: C31.1, IC3.34
unnamed: J2.3, R21.1
unnamed: C27.1, IC2.16
unnamed: C34.1, IC3.29, R16.1
unnamed: Q8.1, Q8.3, R18.2, R20.1
unnamed: Q10.1, Q10.3, R22.2, R24.1
unnamed: R25.2, SJ10.2
unnamed: C33.1, D4.C, D5.C, PS2.3, PS2.4
unnamed: J6.3, R28.1
unnamed: C49.1, IC4.16
unnamed: C53.1, U7.3
unnamed: C53.2, U7.2
unnamed: D9.3, U8.4
unnamed: FL2.2, U6.7
unnamed: FL2.3, U6.6
unnamed: Q17.1, R30.2
unnamed: Q18.1, R29.2
unnamed: C57.2, IC5.31
unnamed: C57.1, IC5.32
unnamed: C58.1, IC5.34
unnamed: C61.1, IC5.29, R32.1
unnamed: Q14.1, Q14.3, R33.2, R35.1
unnamed: Q16.1, Q16.3, R36.2, R38.1
unnamed: R39.2, SJ15.2
unnamed: C60.1, D11.C, D12.C, PS3.3, PS3.4
unnamed: J10.3, R42.1
unnamed: C76.1, IC6.16
unnamed: C80.1, U11.3
unnamed: C80.2, U11.2
unnamed: D15.3, U12.4
unnamed: FL3.2, U10.7
unnamed: FL3.3, U10.6
unnamed: Q23.1, R44.2
unnamed: Q24.1, R43.2
unnamed: C84.2, IC7.31
unnamed: C84.1, IC7.32
unnamed: C85.1, IC7.34
unnamed: C88.1, IC7.29, R46.1
unnamed: Q20.1, Q20.3, R47.2, R49.1
unnamed: Q22.1, Q22.3, R50.2, R52.1
unnamed: R53.2, SJ20.2
unnamed: C87.1, D16.C, D17.C, PS4.3, PS4.4
unnamed: J14.3, R56.1
unnamed: C103.1, IC8.16
unnamed: C107.1, U15.3
unnamed: C107.2, U15.2
unnamed: D20.3, U16.4
unnamed: FL4.2, U14.7
unnamed: FL4.3, U14.6
NEO_OUT: D3.1, J3.3
NEO_OUT1: D9.1, J7.3
NEO_OUT2: D15.1, J11.3
NEO_OUT3: D20.1, J15.3
RESET: C2.1, Q5.3, R4.1, SW1.1, SW1.2, X2.3
RESET1: C29.1, Q11.3, R15.1, SW2.1, SW2.2, X3.3
RESET2: C56.1, Q17.3, R31.1, SW3.1, SW3.2, X9.3
RESET3: C83.1, Q23.3, R45.1, SW4.1, SW4.2, X13.3
RTS: IC2.19, Q5.2, R1.1
RTS1: IC4.19, Q11.2, R3.1
RTS2: IC6.19, Q17.2, R29.1
RTS3: IC8.19, Q23.2, R43.1
RXD0: IC2.21, X2.34
RXD1: IC4.21, X3.34
RXD2: IC6.21, X9.34
RXD3: IC8.21, X13.34
SCK: IC1.14, R21.2, U3.2, X2.13
SCK1: IC3.14, R28.2, U5.2, X3.13
SCK2: IC5.14, R42.2, U9.2, X9.13
SCK3: IC7.14, R56.2, U13.2, X13.13
SCL: J2.7, R17.1, X2.36
SCL1: J6.7, R27.1, X3.36
SCL2: J10.7, R41.1, X9.36
SCL3: J14.7, R55.1, X13.36
SDA: J2.6, R13.1, X2.33
SDA1: J6.6, R26.1, X3.33
SDA2: J10.6, R40.1, X9.33
SDA3: J14.6, R54.1, X13.33
SRAH: IC1.8, R12.2
SRAH1: IC3.8, R24.2
SRAH2: IC5.8, R38.2
SRAH3: IC7.8, R52.2
SRAL: IC1.7, R11.2
SRAL1: IC3.7, R23.2
SRAL2: IC5.7, R37.2
SRAL3: IC7.7, R51.2
SRBH: IC1.9, R9.2
SRBH1: IC3.9, R20.2
SRBH2: IC5.9, R35.2
SRBH3: IC7.9, R49.2
SRBL: IC1.10, R8.2
SRBL1: IC3.10, R19.2
SRBL2: IC5.10, R34.2
SRBL3: IC7.10, R48.2
TMC_DIAG0: IC1.26, X2.5
TMC_DIAG1: IC1.27, X2.4
TMC_DIAG2: IC3.27, X3.4
TMC_DIAG3: IC3.26, X3.5
TMC_DIAG4: IC5.27, X9.4
TMC_DIAG5: IC5.26, X9.5
TMC_DIAG6: IC7.27, X13.4
TMC_DIAG7: IC7.26, X13.5
TXD0: IC2.20, X2.35
TXD1: IC4.20, X3.35
TXD2: IC6.20, X9.35
TXD3: IC8.20, X13.35
USBD+: D7.3, IC2.3, J4.3
USBD+1: D6.3, IC4.3, J8.3
USBD+2: D13.3, IC6.3, J12.3
USBD+3: D18.3, IC8.3, J16.3
USBD-: D7.4, IC2.4, J4.2
USBD-1: D6.4, IC4.4, J8.2
USBD-2: D13.4, IC6.4, J12.2
USBD-3: D18.4, IC8.4, J16.2
VBUS: D1.A, D7.2, IC2.8, J4.1
VBUS1: D4.A, D6.2, IC4.8, J8.1
VBUS2: D11.A, D13.2, IC6.8, J12.1
VBUS3: D16.A, D18.2, IC8.8, J16.1

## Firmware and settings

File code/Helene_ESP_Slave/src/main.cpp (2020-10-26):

#include <Arduino.h>
#include <math.h>
#include "Motor.h" //Das hier ist der TMC5160
#include <AS5048A.h>
#include <ESP32CAN.h>
#include "ws2812.h"
#include <EEPROM.h>
#include <PID_v1.h>
#include <scpiparser.h>

#define PI 3.1415926535897932384626433832795
#define PIN_CS_TMC 15
#define PIN_EN_TMC 16
#define PIN_CS_INT_AMS 17
#define PIN_CS_EXT_AMS 18
#define PIN_NEOPIXEL 32
#define PIN_JOINT_ID_BIT3 33
#define PIN_JOINT_ID_BIT2 25
#define PIN_JOINT_ID_BIT1 26
#define PIN_JOINT_ID_BIT0 27
#define EEPROM_SIZE 64
#define EEPROM_ADDRESS_ENABLE_STARTUP 1    //If the Integer at this Address = 1, the "Nullpunktfahrt" is enabled at startup
#define EEPROM_ADDRESS_AS5048_OFFSET 10    //The magnet Offset is saved at the Adresses 10-13 as long
#define TIME_MS_TIMEOUT_NULLPUNKTFART 7500 //The maximum amount of time per axis for the Nullpunktfahrt.
#define TIME_MS_PUBLISH_FREQUENCY 19 // A bit more than 50Hz
#define TIME_MS_TIMEOUT_STOP 300 //If there is no command for 300ms, the Motor is automatically switched off.

int g_this_joint = 0;

float g_motor_transmission[6] = {3.5, -84.48, -37.77, -4.75, -3, 1};
int g_as_sign[6] = {1, 1, -1, 1, 1, 1};
boolean g_high_motor_current[6] = {1, 1, 1, 0, 1, 0};
int g_enable_Nullpunktfahrt;

long g_target_velocity;
long g_actual_velocity;
long g_actual_angle;
int g_state = 0; //0 = Off+LED_Red; 1 = normal operation; 2 = going to initial position
long g_ms_time_differenze_publish = 0;
uint8_t g_led_rgb[3] = {0, 0, 0};
boolean g_tx_frame_slave2master_send = false; //Is true, when there is a Can-packet, that should be sent.
boolean g_tx_frame_slave2config_send = false; //Is true, when there is a Can-packet, that should be sent.
uint8_t g_ma2sl_led_red;

typedef union { // This structure is used to easily convert 2 long values into 8 uint8_t values for CAN communication
  struct
  {
    long angle;
    long velocity;
  };
  uint8_t data[8];
} convert_ll2c;
convert_ll2c g_slave2master;

typedef union { // This structure is used to easily convert 4 int values and 1 long value into 8 uint8_t values for CAN communication
  struct
  {
    uint8_t operation_ident;
    uint8_t reserved;
    uint8_t led_green;
    uint8_t led_blue;
    long target_velocity;
  };
  uint8_t data[8];
} convert_iiiil2c;
convert_iiiil2c g_master2slave;

typedef union { // This structure is used to easily convert 2 int values and 3 uint16 value into 8 uint8_t values for CAN communication
  struct
  {
    uint8_t operation; //0 is nothing, 1 is save the tobesaved_offset_value, 2 is to start the calibraton sequence, 3 is to end. In the Calibration Sequence the Motor is deactivated! 4 is to enable the Nullpunktfahrt, 5 is to disable, 6 is to answer with the actual Angle (not RAW!), 7 is to do Nullpunkfahrt
    uint8_t answer_to_this;
    uint16_t current_offset_value;
    uint16_t tobesaved_offset_value;
    uint16_t raw_magnet_angle;
  };
  uint8_t data[8];
} convert_config;
convert_config g_platine2config;

CAN_device_t CAN_cfg;
CAN_frame_t g_rx_frame_master2slave;
CAN_frame_t g_tx_frame_slave2master;
CAN_frame_t g_tx_frame_slave2config;
/*
Can ID List: 
2:Master2Slave for Joint 2
3:Master2Slave for Joint 3
4:Master2Slave for Joint 4
5:Master2Slave for Joint 5
6:Master2Slave for Joint 6
12:Slave2Master from Joint 2
13:Slave2Master from Joint 3
14:Slave2Master from Joint 4
15:Slave2Master from Joint 5
16:Slave2Master from Joint 6
21:platine2config to Joint 1
22:platine2config to Joint 2
23:platine2config to Joint 3
24:platine2config to Joint 4
25:platine2config to Joint 5
26:platine2config to Joint 6
27:platine2config to calibrationMaster from the previously adressed Joint
*/

Motor tmc = Motor(PIN_CS_TMC, PIN_EN_TMC, 10000, 10000, false);
AS5048A obj_angleSensor(PIN_CS_INT_AMS);
rgbVal *obj_pixels;
double g_Input_obj_init_PID, g_Output_obj_init_PID, g_Setpoint_obj_init_PID;
PID obj_init_PID(&g_Input_obj_init_PID, &g_Output_obj_init_PID, &g_Setpoint_obj_init_PID, 30, 0.05, 0, P_ON_E, DIRECT);

//SCPI Stuff
struct scpi_parser_context ctx;

scpi_error_t scpi_identify(struct scpi_parser_context *context, struct scpi_token *command);
scpi_error_t scpi_print_help(struct scpi_parser_context *context, struct scpi_token *command);
scpi_error_t scpi_setzenullpunktfahrt(struct scpi_parser_context *context, struct scpi_token *command);
scpi_error_t scpi_get_calvalueofoint(struct scpi_parser_context *context, struct scpi_token *command);
scpi_error_t scpi_get_actlmagvalofjoint(struct scpi_parser_context *context, struct scpi_token *command);
scpi_error_t scpi_get_rawvalofjoint(struct scpi_parser_context *context, struct scpi_token *command);
scpi_error_t scpi_set_calvalueofoint(struct scpi_parser_context *context, struct scpi_token *command);
scpi_error_t scpi_caljoint(struct scpi_parser_context *context, struct scpi_token *command);
scpi_error_t scpi_do_nullpunktfahrt(struct scpi_parser_context *context, struct scpi_token *command);
scpi_error_t scpi_do_offsetandnull(struct scpi_parser_context *context, struct scpi_token *command);
scpi_error_t scpi_get_diag(struct scpi_parser_context *context, struct scpi_token *command);

TaskHandle_t canwriteframe_TaskHnd;

void canwriteframe_Task(void *parameter) //This Task runs on a different core and is only responsible for pushing the can packet
{
  for (;;)
  {
    if (g_tx_frame_slave2master_send == true)
    {
      ESP32Can.CANWriteFrame(&g_tx_frame_slave2master);
      g_tx_frame_slave2master_send = false; // Set it to false afterwards, so that a new message can be sent
    }
    if (g_tx_frame_slave2config_send == true)
    {
      ESP32Can.CANWriteFrame(&g_tx_frame_slave2config);
      g_tx_frame_slave2config_send = false;
    }
    delayMicroseconds(5);
    yield();
  }
}

//This axis does a Nullpunktfahrt
void this_axis_do_Nullpunktfahrt(boolean l_thisjointisatgoal, long l_starttime)
{
  obj_init_PID.SetMode(AUTOMATIC);
  obj_init_PID.SetOutputLimits(-5000, 5000);
  //obj_init_PID.SetSampleTime(9);
  g_Setpoint_obj_init_PID = 8192;
  if (g_this_joint == 3)
  {
    g_Setpoint_obj_init_PID = 8192 + 4096;
  }
  while (l_thisjointisatgoal == false && millis() - l_starttime < TIME_MS_TIMEOUT_NULLPUNKTFART) //PID Regler zum erreichen des Nullpunkts
  {
    obj_pixels[0] = makeRGBVal(0, 125 + 125 * sin(millis() / 50), 0);
    ws2812_setColors(1, obj_pixels);
    g_Input_obj_init_PID = double((obj_angleSensor.getRotation() * g_as_sign[g_this_joint - 1] + 8192));
    obj_init_PID.Compute();
    //Serial.println("Pos: " + String(g_Input_obj_init_PID) + "  I-Summe: " + String(obj_init_PID.GetOutputSum()));
    tmc.set_velocity(long(g_Output_obj_init_PID * g_motor_transmission[g_this_joint - 1]));
    int angle = obj_angleSensor.getRotation();
    if (g_this_joint == 3)
    {
      angle = angle + 4096;
    }
    if (abs(angle) < 10 && abs(tmc.get_vtarget()) < abs(25 * g_motor_transmission[g_this_joint - 1]))
    { //Goal is reached
      tmc.set_velocity(0);
      l_thisjointisatgoal = true;
    }
    delay(10);
  }
  obj_pixels[0] = makeRGBVal(0, 0, 0);
  ws2812_setColors(1, obj_pixels);
}

void setup()
{
  tmc.disable_motor();
  pinMode(PIN_CS_INT_AMS, OUTPUT);
  pinMode(PIN_CS_EXT_AMS, OUTPUT);
  pinMode(PIN_JOINT_ID_BIT3, INPUT_PULLUP);
  pinMode(PIN_JOINT_ID_BIT2, INPUT_PULLUP);
  pinMode(PIN_JOINT_ID_BIT1, INPUT_PULLUP);
  pinMode(PIN_JOINT_ID_BIT0, INPUT_PULLUP);
  digitalWrite(PIN_CS_INT_AMS, HIGH);
  digitalWrite(PIN_CS_EXT_AMS, HIGH);
  delay(1);

  //Decode the Joint-ID
  g_this_joint = !digitalRead(PIN_JOINT_ID_BIT0) * 1 + !digitalRead(PIN_JOINT_ID_BIT1) * 2 + !digitalRead(PIN_JOINT_ID_BIT2) * 4 + !digitalRead(PIN_JOINT_ID_BIT3) * 8;

  //All slaves are configured, to be able to configure all zeroPositions from all joints. To start the calibration, the serial interface is necessary
  Serial.begin(115200);
  Serial.println(String(F("Started Slave. Joint = ")) + String(g_this_joint));

  //SCPI initialisation
  scpi_init(&ctx);
  /*
  IDN?         -> identify (done)
  CAlsingleJOint 
  SEtNUll
  GEtCAlvalue
  */
  //Allgemein
  scpi_register_command(ctx.command_tree, SCPI_CL_SAMELEVEL, "*IDN?", 5, "IDN?", 4, scpi_identify);
  scpi_register_command(ctx.command_tree, SCPI_CL_SAMELEVEL, "HELP?", 5, "HELP", 4, scpi_print_help);
  scpi_register_command(ctx.command_tree, SCPI_CL_SAMELEVEL, "CALSINGLEJOINT", 14, "CAJO", 4, scpi_caljoint);
  scpi_register_command(ctx.command_tree, SCPI_CL_SAMELEVEL, "SETNULL", 7, "SENU", 4, scpi_setzenullpunktfahrt);
  scpi_register_command(ctx.command_tree, SCPI_CL_SAMELEVEL, "GETCALVALUE", 11, "GECA", 4, scpi_get_calvalueofoint);
  scpi_register_command(ctx.command_tree, SCPI_CL_SAMELEVEL, "SETCALVALUE", 11, "SECA", 4, scpi_set_calvalueofoint);
  scpi_register_command(ctx.command_tree, SCPI_CL_SAMELEVEL, "GETACTUAL", 9, "GEAC", 4, scpi_get_actlmagvalofjoint);
  scpi_register_command(ctx.command_tree, SCPI_CL_SAMELEVEL, "GETRAW", 6, "GERA", 4, scpi_get_rawvalofjoint);
  scpi_register_command(ctx.command_tree, SCPI_CL_SAMELEVEL, "DONULL", 6, "DONU", 4, scpi_do_nullpunktfahrt);
  scpi_register_command(ctx.command_tree, SCPI_CL_SAMELEVEL, "OFFANDNULL", 10, "OFNU", 4, scpi_do_offsetandnull);
  scpi_register_command(ctx.command_tree, SCPI_CL_SAMELEVEL, "DIAG", 4, "DIA", 3, scpi_get_diag);

  //Neopixel initialisation
  ws2812_init(PIN_NEOPIXEL, LED_WS2812B);
  obj_pixels = (rgbVal *)malloc(sizeof(rgbVal) * 1); //1 ist die Anzahl der Neopixel. Wir haben halt nur einen
  obj_pixels[0] = makeRGBVal(255, 0, 0);             // Rot am Anfang
  ws2812_setColors(1, obj_pixels);

  //Check if JointID is valid
  if (g_this_joint == 0 || g_this_joint == 1 || g_this_joint > 6)
  {
    Serial.println(String(F("Invalid Joint ID!")));
    while (true)
    {
      obj_pixels[0] = makeRGBVal(255, 0, 0);
      ws2812_setColors(1, obj_pixels);
      delay(200);
      obj_pixels[0] = makeRGBVal(0, 0, 0);
      ws2812_setColors(1, obj_pixels);
      delay(2000);
    }
  }

  //CAN initialisation. We start the CAN Interface with 500kbps, using GPIOs 4 and 5 and with a que of 100 elements
  CAN_cfg.rx_queue = xQueueCreate(100, sizeof(CAN_frame_t));
  CAN_cfg.speed = CAN_SPEED_200KBPS;
  CAN_cfg.tx_pin_id = GPIO_NUM_5;
  CAN_cfg.rx_pin_id = GPIO_NUM_4;
  ESP32Can.CANInit();

  //Start the EEprom
  EEPROM.begin(EEPROM_SIZE);

  //Read the important EEprom values
  g_enable_Nullpunktfahrt = EEPROM.read(EEPROM_ADDRESS_ENABLE_STARTUP);
  uint16_t l_ASoffset = EEPROM.readShort(EEPROM_ADDRESS_AS5048_OFFSET);

  //Check if the values are valid. If not overwrite the saved values
  if (g_enable_Nullpunktfahrt != 0 && g_enable_Nullpunktfahrt != 1)
  { //Overwrite if wrong
    g_enable_Nullpunktfahrt = 0;
    EEPROM.write(EEPROM_ADDRESS_ENABLE_STARTUP, 0);
    EEPROM.commit();
  }
  if (l_ASoffset > (16384))
  { // Overwrite if Offset is to high
    l_ASoffset = 0;
    EEPROM.writeShort(EEPROM_ADDRESS_AS5048_OFFSET, 0);
    EEPROM.commit();
  }

  //Start the magnetic rotary encoder and set the zero Position
  obj_angleSensor.init();
  obj_angleSensor.setZeroPosition(l_ASoffset);
  //check if the angle sensor works
  boolean l_boolean_isnotzero = false;
  for(int i=0; i< 20; i++){ //One Reading in 20 should not be 0 due to noise. If not -> Sensor is missing!
    if(obj_angleSensor.getRawRotation() != 0){
      l_boolean_isnotzero = true;
    }
  }
  if(l_boolean_isnotzero == false)//If all values have been 0 -> Error blinking
  {
    while (true)
    {
      obj_pixels[0] = makeRGBVal(255, 0, 0);
      ws2812_setColors(1, obj_pixels);
      delay(200);
      obj_pixels[0] = makeRGBVal(0, 0, 0);
      ws2812_setColors(1, obj_pixels);
      delay(200);
      obj_pixels[0] = makeRGBVal(255, 0, 0);
      ws2812_setColors(1, obj_pixels);
      delay(200);
      obj_pixels[0] = makeRGBVal(0, 0, 0);
      ws2812_setColors(1, obj_pixels);
      delay(2000);
    }
  }

  //Set the motor current and enable motor. However it would not be great, if all motors would start at the same time. So first axis 1, then 2, then 3... are started.
  for (int i = 0; i < g_this_joint; i++)
  {
    obj_pixels[0] = makeRGBVal(0, 0, 255);
    ws2812_setColors(1, obj_pixels);
    delay(200);
    obj_pixels[0] = makeRGBVal(0, 0, 0);
    ws2812_setColors(1, obj_pixels);
    delay(200);
  }
  tmc.enable_motor();
  tmc.set_current(g_high_motor_current[g_this_joint - 1]);
  if (g_this_joint == 2 || g_this_joint == 3)
  { //Higher acceleration if axis 2 or 3. Due to the high transmission!
    tmc.set_acceleration(10000 * abs(g_motor_transmission[g_this_joint - 1]));
  }
  for (int i = g_this_joint; i < 6; i++)
  {
    delay(400);
  }
  obj_pixels[0] = makeRGBVal(255, 0, 0);
  ws2812_setColors(1, obj_pixels);

  //The function ESP32Can.CANWriteFrame is blocking, when an error occours. For that reason, a new task is created, so that the main program still functions.
  xTaskCreatePinnedToCore(canwriteframe_Task, "canwriteframe_Task", 5000, NULL, 1, &canwriteframe_TaskHnd, 0);

  disableCore0WDT();
  //disableCore1WDT();

  //Wait a bit to settle
  delay(100);
}

void loop()
{
  while (xQueueReceive(CAN_cfg.rx_queue, &g_rx_frame_master2slave, 0) == pdTRUE) //I just received a CAN-packet
  {
    if (g_rx_frame_master2slave.FIR.B.RTR != CAN_RTR && g_rx_frame_master2slave.MsgID == g_this_joint) //I received a command package
    {
      g_master2slave.data[0] = g_rx_frame_master2slave.data.u8[0];
      g_master2slave.data[1] = g_rx_frame_master2slave.data.u8[1];
      g_master2slave.data[2] = g_rx_frame_master2slave.data.u8[2];
      g_master2slave.data[3] = g_rx_frame_master2slave.data.u8[3];
      g_master2slave.data[4] = g_rx_frame_master2slave.data.u8[4];
      g_master2slave.data[5] = g_rx_frame_master2slave.data.u8[5];
      g_master2slave.data[6] = g_rx_frame_master2slave.data.u8[6];
      g_master2slave.data[7] = g_rx_frame_master2slave.data.u8[7];
      g_target_velocity = g_master2slave.target_velocity * g_motor_transmission[g_this_joint - 1];
      g_state = g_master2slave.operation_ident;
      g_ma2sl_led_red = 0;
      boolean l_thisjointisatgoal = false; //I cant initialise variables inside the switch-routine (Thanks C)
      long l_starttime = millis();
      switch (g_state)
      {
      case 0:
        tmc.set_velocity(0);
        break;
      case 1:
        tmc.set_velocity(g_target_velocity);
        break;
      case 2:
        if (g_enable_Nullpunktfahrt == 1) //case 2 is to do the Nullpunktfahrt. Only start it, if globally enabled!
        {
          this_axis_do_Nullpunktfahrt(l_thisjointisatgoal, l_starttime);
        }
        else
        {
          tmc.set_velocity(0);
        }
        g_state = 0;
        break;
      default:
        tmc.set_velocity(0);
        break;
      }
    }
    else if (g_rx_frame_master2slave.FIR.B.RTR != CAN_RTR && g_rx_frame_master2slave.MsgID == 20 + g_this_joint) //I received a config packet for this specific axis
    {
      g_platine2config.data[0] = g_rx_frame_master2slave.data.u8[0];
      g_platine2config.data[1] = g_rx_frame_master2slave.data.u8[1];
      g_platine2config.data[2] = g_rx_frame_master2slave.data.u8[2];
      g_platine2config.data[3] = g_rx_frame_master2slave.data.u8[3];
      g_platine2config.data[4] = g_rx_frame_master2slave.data.u8[4];
      g_platine2config.data[5] = g_rx_frame_master2slave.data.u8[5];
      g_platine2config.data[6] = g_rx_frame_master2slave.data.u8[6];
      g_platine2config.data[7] = g_rx_frame_master2slave.data.u8[7];
      boolean l_thisjointisatgoal = false; //I cant initialise variables inside the switch-routine (Thanks C)
      long l_starttime = millis();
      //g_platine2config.operation: 0 is nothing, 1 is save the tobesaved_offset_value, 2 is to start the calibraton sequence, 3 is to end. In the Calibration Sequence the Motor is deactivated! 4 is to enable the Nullpunktfahrt, 5 is to disable, 6 is to send actual Position instead of raw, 7 is to do Nullpunktfahrt.
      switch (g_platine2config.operation)
      {
      case 1:
        EEPROM.writeShort(EEPROM_ADDRESS_AS5048_OFFSET, g_platine2config.tobesaved_offset_value);
        EEPROM.commit();
        obj_angleSensor.setZeroPosition(g_platine2config.tobesaved_offset_value);
        break;
      case 2:
        tmc.disable_motor();
        break;
      case 3:
        tmc.enable_motor();
        break;
      case 4:
        g_enable_Nullpunktfahrt = 1;
        EEPROM.write(EEPROM_ADDRESS_ENABLE_STARTUP, 1);
        EEPROM.commit();
        break;
      case 5:
        g_enable_Nullpunktfahrt = 0;
        EEPROM.write(EEPROM_ADDRESS_ENABLE_STARTUP, 0);
        EEPROM.commit();
        break;
      case 7:
        this_axis_do_Nullpunktfahrt(l_thisjointisatgoal, l_starttime);
        break;
      default:
        break;
      }
      if (g_platine2config.answer_to_this == 1)
      {
        g_platine2config.current_offset_value = EEPROM.readShort(EEPROM_ADDRESS_AS5048_OFFSET);
        if (g_platine2config.operation == 6)
        {
          g_platine2config.raw_magnet_angle = obj_angleSensor.getRotation();
        }
        else
        {
          g_platine2config.raw_magnet_angle = obj_angleSensor.getRawRotation();
        }
        g_tx_frame_slave2config.data.u8[0] = g_platine2config.data[0];
        g_tx_frame_slave2config.data.u8[1] = g_platine2config.data[1];
        g_tx_frame_slave2config.data.u8[2] = g_platine2config.data[2];
        g_tx_frame_slave2config.data.u8[3] = g_platine2config.data[3];
        g_tx_frame_slave2config.data.u8[4] = g_platine2config.data[4];
        g_tx_frame_slave2config.data.u8[5] = g_platine2config.data[5];
        g_tx_frame_slave2config.data.u8[6] = g_platine2config.data[6];
        g_tx_frame_slave2config.data.u8[7] = g_platine2config.data[7];
        g_tx_frame_slave2config.FIR.B.FF = CAN_frame_std;
        g_tx_frame_slave2config.MsgID = 27;
        g_tx_frame_slave2config.FIR.B.DLC = 8;
        g_tx_frame_slave2config_send = true;
      }
    }
  }
  if (millis() - g_ms_time_differenze_publish >= TIME_MS_PUBLISH_FREQUENCY) //Checke if Failsafe notwendig ist und sende einen CAN Frame zum Master mit den aktuellen Daten
  {
    g_ms_time_differenze_publish = millis();
    if (millis() - tmc.get_last_time_of_set_velocity() > TIME_MS_TIMEOUT_STOP && (g_state == 1 || g_state == 0))
    { //Failsafe!
      g_target_velocity = 0;
      if (tmc.get_vtarget() != 0)
      {
        tmc.set_velocity(g_target_velocity);
      }
      g_master2slave.led_green = 0;
      g_master2slave.led_blue = 0;
      g_ma2sl_led_red = 255;
    }

    if (g_tx_frame_slave2master_send == false) //Wenn nix gesendet wird, dann baue ich einen neuen CAN-Frame! Und sende ihn
    {
      g_slave2master.velocity = tmc.get_vactual() / g_motor_transmission[g_this_joint - 1];
      g_slave2master.angle = obj_angleSensor.getRotation() * g_as_sign[g_this_joint - 1];
      g_tx_frame_slave2master.FIR.B.FF = CAN_frame_std;
      g_tx_frame_slave2master.MsgID = g_this_joint + 10;
      g_tx_frame_slave2master.FIR.B.DLC = 8;
      g_tx_frame_slave2master.data.u8[0] = g_slave2master.data[0];
      g_tx_frame_slave2master.data.u8[1] = g_slave2master.data[1];
      g_tx_frame_slave2master.data.u8[2] = g_slave2master.data[2];
      g_tx_frame_slave2master.data.u8[3] = g_slave2master.data[3];
      g_tx_frame_slave2master.data.u8[4] = g_slave2master.data[4];
      g_tx_frame_slave2master.data.u8[5] = g_slave2master.data[5];
      g_tx_frame_slave2master.data.u8[6] = g_slave2master.data[6];
      g_tx_frame_slave2master.data.u8[7] = g_slave2master.data[7];
      g_tx_frame_slave2master_send = true;
    }

    if (g_led_rgb[0] != g_ma2sl_led_red || g_led_rgb[1] != g_master2slave.led_green || g_led_rgb[2] != g_master2slave.led_blue) //Leds setzen
    {
      g_led_rgb[0] = g_ma2sl_led_red;
      g_led_rgb[1] = g_master2slave.led_green;
      g_led_rgb[2] = g_master2slave.led_blue;
      //Print LED Values here!
      obj_pixels[0] = makeRGBVal(g_led_rgb[0], g_led_rgb[1], g_led_rgb[2]);
      ws2812_setColors(1, obj_pixels);
    }
  }
  yield();
  if (Serial.available() > 0) //Hier schaue ich ob Serielle Daten Kommen & wenn ja dann wird der Befehl nach SCPI durchsucht
  {
    char line_buffer[128];
    unsigned char read_length;
    /* Read in a line and execute it. */
    read_length = Serial.readBytesUntil('\n', line_buffer, 128);
    if (read_length > 0)
    {
      scpi_execute_command(&ctx, line_buffer, read_length);
    }
  }
}

void setPowerstateofJoint(int jointid, boolean powerstate) //This function either activates or deactivates the motor of one joint. If powerstate == true the motor gets activated.
{
  long l_starttime = millis();
  boolean l_igottotransmit = false;
  g_platine2config.answer_to_this = 0;
  ;
  // g_platine2config.operation 2 is to start the calibraton sequence, 3 is to end
  if (powerstate == true)
  {
    g_platine2config.operation = 3;
  }
  else
  {
    g_platine2config.operation = 2;
  }
  while (l_igottotransmit == false && millis() - l_starttime < 500)
  {
    if (g_tx_frame_slave2master_send == false) //Wenn nix gesendet wird, dann baue ich einen neuen CAN-Frame! Und sende ihn
    {
      g_tx_frame_slave2master.FIR.B.FF = CAN_frame_std;
      g_tx_frame_slave2master.MsgID = 20 + jointid;
      g_tx_frame_slave2master.FIR.B.DLC = 8;
      g_tx_frame_slave2master.data.u8[0] = g_platine2config.data[0];
      g_tx_frame_slave2master.data.u8[1] = g_platine2config.data[1];
      g_tx_frame_slave2master.data.u8[2] = g_platine2config.data[2];
      g_tx_frame_slave2master.data.u8[3] = g_platine2config.data[3];
      g_tx_frame_slave2master.data.u8[4] = g_platine2config.data[4];
      g_tx_frame_slave2master.data.u8[5] = g_platine2config.data[5];
      g_tx_frame_slave2master.data.u8[6] = g_platine2config.data[6];
      g_tx_frame_slave2master.data.u8[7] = g_platine2config.data[7];
      g_tx_frame_slave2master_send = true;
      l_igottotransmit = true;
    }
  }
  if (l_igottotransmit == false)
  {
    Serial.println("Unable to transmit CAN Package");
  }
}
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

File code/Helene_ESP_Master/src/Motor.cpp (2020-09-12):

#include "Motor.h"

void Motor::send_Data(unsigned long address, unsigned long datagram)
{
  uint8_t stat;
  unsigned long i_datagram;
  SPI.beginTransaction(tmc_spi_settings);

  digitalWrite(g_chipCS, LOW);
  delayMicroseconds(10);

  stat = SPI.transfer(address);

  i_datagram |= SPI.transfer((datagram >> 24) & 0xff);
  i_datagram <<= 8;
  i_datagram |= SPI.transfer((datagram >> 16) & 0xff);
  i_datagram <<= 8;
  i_datagram |= SPI.transfer((datagram >> 8) & 0xff);
  i_datagram <<= 8;
  i_datagram |= SPI.transfer((datagram)&0xff);
  digitalWrite(g_chipCS, HIGH);
  SPI.endTransaction();
}

Motor::Motor(int CS, int EN, long u_maxspeed, long u_acceleration, boolean u_highcurrent)
{
  g_chipCS = CS;
  g_max_speed = u_maxspeed;
  g_acceleration = u_acceleration;
  pinMode(g_chipCS, OUTPUT);
  pinMode(EN, OUTPUT);
  g_pin_en = EN;
  digitalWrite(g_pin_en,HIGH);
  tmc_spi_settings = SPISettings(4000000, MSBFIRST, SPI_MODE3);
  SPI.begin(14, 12, 13, 9);
  send_Data(0xA0, 0);
  send_Data(0x80, 0x00000000);     //GCONF
  send_Data(0xEC, 0x000101D5);     //CHOPCONF: TOFF=5, HSTRT=5, HEND=3, TBL=2, CHM=0 (spreadcycle)
  if(u_highcurrent==true){
      send_Data(0x90,0x0006070A);
  }else{
      send_Data(0x90,0x00060304);
  }
  send_Data(0x91, 0x0000000A);     //TPOWERDOWN=10
  send_Data(0xF0, 0x00000000);     // PWMCONF
  send_Data(0xA4, g_acceleration); //A1=1000
  send_Data(0xA5, g_max_speed);    //V1=100000
  send_Data(0xA6, g_acceleration); //AMAX=50000
  send_Data(0xA7, g_max_speed);    //VMAX=500000
  send_Data(0xAA, 100000);         //D1=1400
  send_Data(0xA8, 100000);         //DMAX=50000
  send_Data(0xAB, 0x0000000A);     //VSTOP=10
  send_Data(0xA0, 0);              //RAMPMODE=0 - bedeutet position-interface. Bei 1 velocity Interface. Die Geschwindigkeit wird dann über VMax gesteuert
  send_Data(0xA1, 0x00000000);     //XACTUAL=0
  send_Data(0xAD, 0x00000000);     //XTARGET=0
  delay(20);
}

long Motor::get_vactual()
{
  uint8_t stat;
  long i_datagram;
  SPI.beginTransaction(tmc_spi_settings);
  digitalWrite(g_chipCS, LOW);
  delayMicroseconds(1);
  SPI.transfer(0x22);
  SPI.transfer(0x00);
  SPI.transfer(0x00);
  SPI.transfer(0x00);
  SPI.transfer(0x00);
  digitalWrite(g_chipCS, HIGH);
  SPI.endTransaction();

  delayMicroseconds(1);

  SPI.beginTransaction(tmc_spi_settings);
  digitalWrite(g_chipCS, LOW);
  delayMicroseconds(1);
  stat = SPI.transfer(0x22);
  i_datagram |= SPI.transfer(0x00);
  i_datagram <<= 8;
  i_datagram |= SPI.transfer(0x00);
  i_datagram <<= 8;
  i_datagram |= SPI.transfer(0x00);
  i_datagram <<= 8;
  i_datagram |= SPI.transfer(0x00);
  digitalWrite(g_chipCS, HIGH);
  SPI.endTransaction();

  if (i_datagram > 8387800)
  { //8387800 ist die häflte einer 3byte Long -> Das vorzeichen wird so hingetrickst!
    i_datagram = i_datagram - 16775600 - 1616;
  }

  return i_datagram;
}

long Motor::get_vtarget()
{
  return g_target_velocity;
}

long Motor::get_xactual()
{
  uint8_t stat;
  long i_datagram;
  SPI.beginTransaction(tmc_spi_settings);
  digitalWrite(g_chipCS, LOW);
  delayMicroseconds(1);
  SPI.transfer(0x21);
  SPI.transfer(0x00);
  SPI.transfer(0x00);
  SPI.transfer(0x00);
  SPI.transfer(0x00);
  digitalWrite(g_chipCS, HIGH);
  SPI.endTransaction();

  delayMicroseconds(1);

  SPI.beginTransaction(tmc_spi_settings);
  digitalWrite(g_chipCS, LOW);
  delayMicroseconds(1);
  stat = SPI.transfer(0x21);
  i_datagram |= SPI.transfer(0x00);
  i_datagram <<= 8;
  i_datagram |= SPI.transfer(0x00);
  i_datagram <<= 8;
  i_datagram |= SPI.transfer(0x00);
  i_datagram <<= 8;
  i_datagram |= SPI.transfer(0x00);
  digitalWrite(g_chipCS, HIGH);
  SPI.endTransaction();

  if (i_datagram > 8387800)
  { //8387800 ist die häflte einer 3byte Long -> Das vorzeichen wird so hingetrickst!
    i_datagram = i_datagram - 16775600 - 1616;
  }

  return i_datagram;
}

void Motor::set_velocity(long datagram)
{
  g_lastcall = millis();
  g_target_velocity = datagram;
  if (abs(datagram) < 1)
  {
    send_Data(0xA7, 0);
  }
  else if (datagram < 0)
  {
    send_Data(0xA0, 2);
    send_Data(0xA7, -datagram); 
  }
  else
  {
    send_Data(0xA0, 1);
    send_Data(0xA7, datagram);  
  }
}

void Motor::set_position(long datagram)
{
  send_Data(0xA0, 0);
  send_Data(0xAD, datagram * 256); 
}

void Motor::set_maxspeed(long datagram)
{
  g_max_speed = datagram;
  send_Data(0xA5, g_max_speed); 
  send_Data(0xA7, g_max_speed); 
}

void Motor::set_acceleration(long datagram)
{
  g_acceleration = datagram;
  send_Data(0xA4, g_acceleration); 
  send_Data(0xA6, g_acceleration); 
}

long Motor::get_last_time_of_set_velocity(){
  return g_lastcall;
}

void Motor::set_current(boolean u_highcurrent)
{
  if(u_highcurrent==true){
      send_Data(0x90,0x0006070A);
  }else{
      send_Data(0x90,0x00060304);
  }
}

void Motor::enable_motor()
{
  digitalWrite(g_pin_en,LOW);
}

void Motor::disable_motor()
{
  digitalWrite(g_pin_en,HIGH);
}

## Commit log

2020-07-21 Added the existing stuff
    [022032021.stp, 10118193-0001LF--3DModel-STEP-56544.STEP, 10147605-8P.stp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]
2020-08-22 Changed folder structure
    [022032021.stp, 10118193-0001LF--3DModel-STEP-56544.STEP, 10147605-8P.stp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]
2020-08-29 Added Getactualpos, Fixed the Nullpunktfahrt and many bug fixes
    [main.cpp]
2020-09-01 Fixed BOM
    [BOM.xlsx, MotorsteuerungV3.xlsx]
2020-09-03 Fixed Motor Currents, Added DONU, GERA
    [Motor.cpp, main.cpp]
2020-09-04 Production Files
    [022032021.stp, 10118193-0001LF--3DModel-STEP-56544.STEP, 10147605-8P.stp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]
2020-09-12 Fixed the calibration, added some SCPI functions
    [022032021.stp, 10118193-0001LF--3DModel-STEP-56544.STEP, 10147605-8P.stp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]
2020-09-22 Label motor control board
2020-10-22 Added optional external H-Bridge
    [BOM_HBridge.xlsx, Digikey_Bom.csv, opt_H_Bridge.brd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]
2021-05-16 Added end-effector pcb and example code. Also fixed the gitignore
    [022032021.stp, 10118193-0001LF--3DModel-STEP-56544.STEP, 10147605-8P.stp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]
2021-05-16 I fucked it up. Firmware is fixed now // Typo!
    [main.cpp]
2025-06-17 Replaced Level Shifter for LEDs. Thanks to Yu-Lien Fang for noticing!
    [42mm_Erweiterungsplatine.brd, 42mm_Erweiterungsplatine.sch, BOM.xlsx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]
2025-06-17 Also changed PDF of schematics

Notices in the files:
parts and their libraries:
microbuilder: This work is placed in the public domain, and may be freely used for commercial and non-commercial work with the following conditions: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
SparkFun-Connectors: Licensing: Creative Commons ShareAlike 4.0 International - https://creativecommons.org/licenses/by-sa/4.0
